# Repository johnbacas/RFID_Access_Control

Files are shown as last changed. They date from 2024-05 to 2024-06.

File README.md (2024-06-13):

## **RFID Access control Project**

Περιγραφή: Το σύστημα αυτό είναι σχεδιασμένο ώστε να κάνει έλεγχο πρόσβασης με χρήση RFID tags.
Η μονάδα ελέγχου που χρησιμοποιείται είναι η πλακέτα NodeMCU με τον μικροελεγκτή (SoC) ESP8266 με δυνατότητα σύνδεσης στο Internet μέσω WiFi.

[Πληροφορίες για esp8266](https://www.espressif.com/en/products/socs/esp8266)

[Πληροφορίες για NodeMCU](https://www.nodemcu.com/index_en.html)

Σαν RFID reader χρησιμοποιήθηκε το module RC-522

[Πληροφορίες για RFID RC-522](https://lastminuteengineers.com/how-rfid-works-rc522-arduino-tutorial/)

**ΠΡΟΣΟΧΗ...!!!**
Αποθήκευση ετικετών: Επειδή ο μικροελεγκτής esp8266 **δεν έχει** μνήμη EEPROM, όλες οι εγγραφές που φαίνεται στο πρόγραμμα ότι γίνονται σε EEPROM στην πραγματικότητα γίνονται στη μνήμη Flash του μικροελεγκτή (Η μνήμη στην οποία αποθηκεύεται και το πρόγραμμα).
Αυτό σημαίνει ότι οι επαναλαμβανόμενες εγγραφές στη μνήμη EEPROΜ φθείρουν τη μνήμη Flash.
Άρα το project αυτό καλό είναι να χρησιμοποιείται σε εφαρμογές όπου δεν θα γίνονται συχνά εγγραφές στη μνήμη EEPROM (Flash).

Δείτε περισσότερες πληροφορίες [εδώ](https://www.aranacorp.com/en/using-the-eeprom-with-the-esp8266/).

Υπάρχουν κάποιες βιβλιοθήκες που ελαχιστοποιούν τη φθορά της μνήμης Flash. Δείτε μια λύση [εδώ](https://www.arduino.cc/reference/en/libraries/esp_eeprom/).

**Α) Λειτουργία προγραμματισμού: ( το μπλε led αναβοσβήνει με γρήγορο ρυθμό)**

 - Ορισμός master tag

Ο εγκαταστάστης του συστήματος έχει τη δυνατότητα να ορίσει ένα master tag, μέσω του οποίου μπορεί να προσθέτει και να αφαιρεί tags από την λίστα των tags που έχουν πρόσβαση.
Όταν το σύστημα τίθεται σε λειτουργία την πρώτη φορά, ζητάει από τον προγραμματιστή να ορίσει ποιο είναι το *master tag*. Στη συνέχεια ο προγραμματιστής πλησιάζει στο RFID Reader το tag που θέλει να ορίσει σαν master. Το master tag αποθηκεύεται στη μνήμη του συστήματος.

 - Προσθήκη ή αφαίρεση tag από την λίστα πρόσβασης

Ο προγραμματιστής αρχικά χρησιμοποιεί το master tag για να μπει σε programming mode. Στη συνέχεια πλησιάζει στον reader ένα tag. Αν αυτό δεν υπάρχει στη λίστα πρόσβασης τότε προστίθεται (το πράσινο led αναβοσβήνει 3 φορές) , ενώ αν υπάρχει τότε αφαιρείται ( τα μπλε και πράσινο leds αναβοσβήνουν 3 φορές). Αν για κάποιο λόγο η εγγραφή δεν πραγματοποιηθεί τότε το μπλε led αναβοσβήνει 3 φορές και το buzzer ηχεί 3 φορές επίσης.

**Β) Λειτουργία ελέγχου πρόσβασης: ( το μπλε led αναβοσβήνει με αργό ρυθμό)**

Ο χρήστης πλησιάζει το tag του στον reader. Αν το σύστημα έχει αποθηκευμένο τον κωδικό του tag αυτού τότε δίνει εντολή ώστε να δωθεί πρόσβαση (μεσω της ενεργοποίησης της ηλεκτρικής κλειδαριάς). Αν ο κωδικός δεν είναι αποθηκευμένος, το σύστημα ενημερώνει με ήχο τον χρήστη ότι δεν έχει πρόσβαση.

Ανεξαρτήτως λειτουργίας, κάθε φορά που διαβάζεται ένα tag από τον reader το πράσινο led ανάβει για 0,5 sec.

SCHEMATIC:

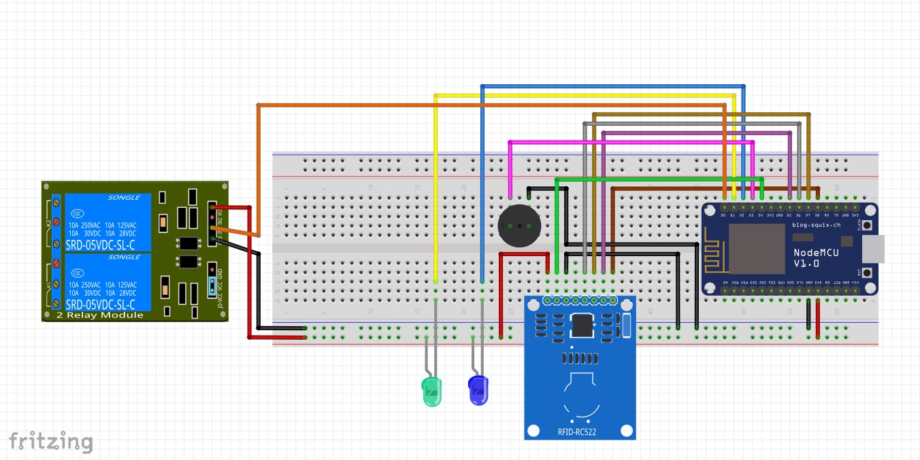
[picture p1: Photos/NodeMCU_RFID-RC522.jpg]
RFID_Access_Control_Img


**Blynk Console - Εφαρμογή ειδοποιήσεων και καταγραφής των περιστατικών προσπάθειας πρόσβασης**

Ο εγκαταστάστης του συστήματος έχει πρόσβαση στο περιβάλλον Blynk (Πλατφόρμα εφαρμογών IOT). Στο dashboard υπάρχει widget τύπου terminal που καταγράφει τα περιστατικά προσπάθειας πρόσβασης.
Στο terminal καταγράφονται η ημερομηνία και η ώρα της πρόσβασης, και αν η πρόσβαση ήταν επιτυχής ή οχι. Επίσης γίνεται καταγραφή της χρήσης master card στο σύστημα.
Παρακάτω φαίνεται ένα παράδειγμα καταγραφής.

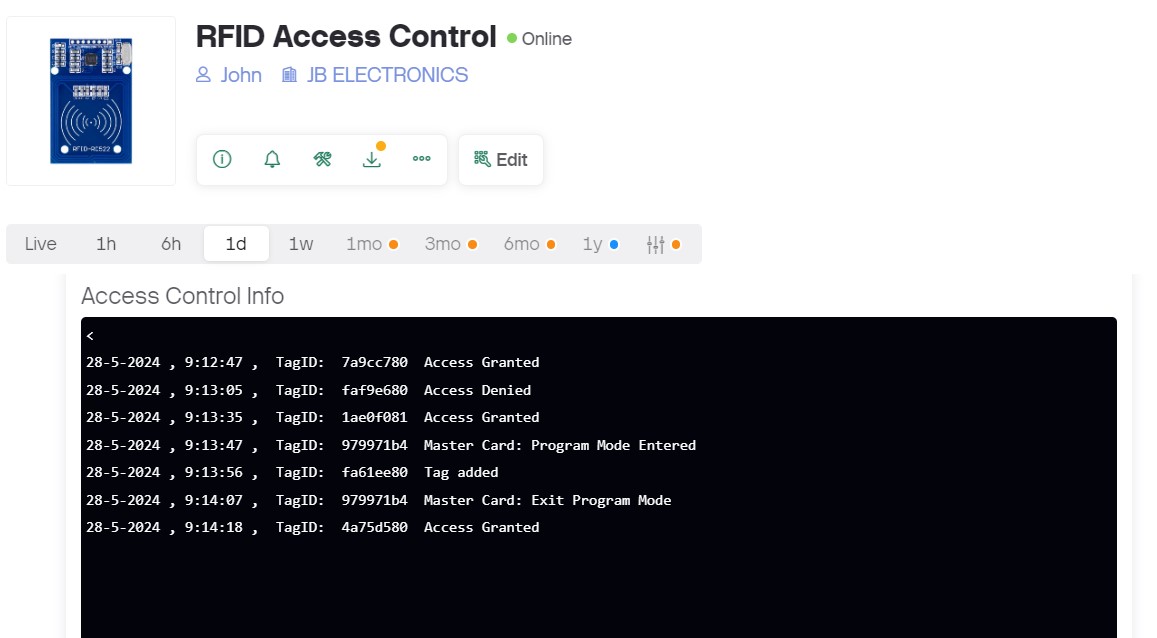
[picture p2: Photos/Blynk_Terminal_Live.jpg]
Blynk Terminal


Για να δημιουργήσετε το συσγκεκριμένο dashboard θα πρέπει να δημιουργήσετε ένα λογαρισμό στην εφαρμογή Blynk και στη συνέχεια, μπαίνοντας στο developer zone, να δημιουργήσετε ένα νεο template και στη συνέχεια ένα νεο Device.
Εισάγετε το widget Terminal με τις παρακάτω ρυθμίσεις.

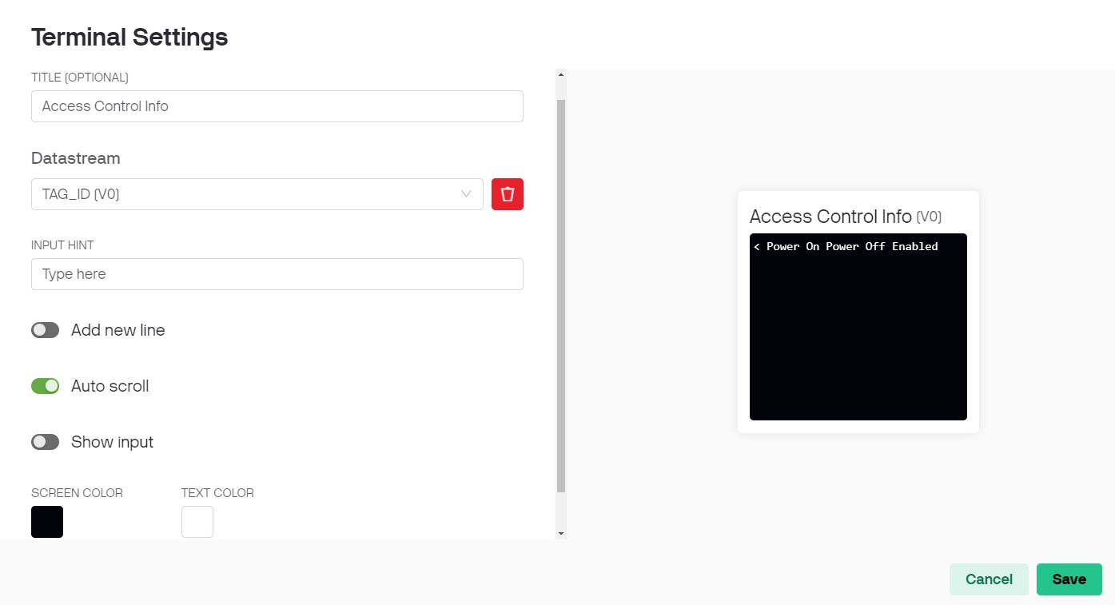
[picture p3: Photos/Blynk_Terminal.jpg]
Blynk Terminal Configure


Επίσης, μην ξεχάσετε να προσθέσετε και ένα event ώστε να έχετε logging υπηρεσία στην εφαρμογή σας.

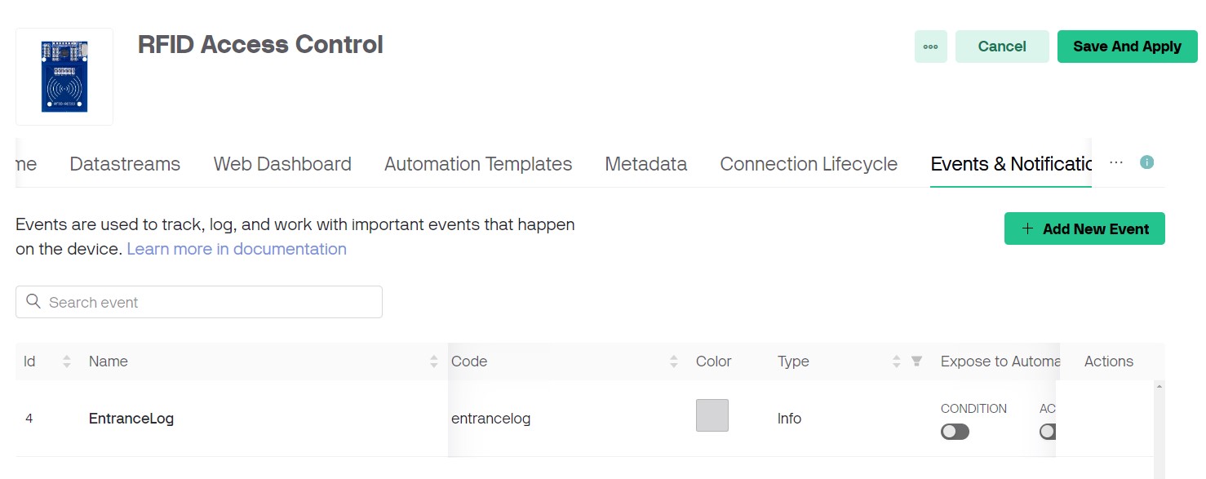
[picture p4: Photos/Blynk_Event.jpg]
Blynk Event


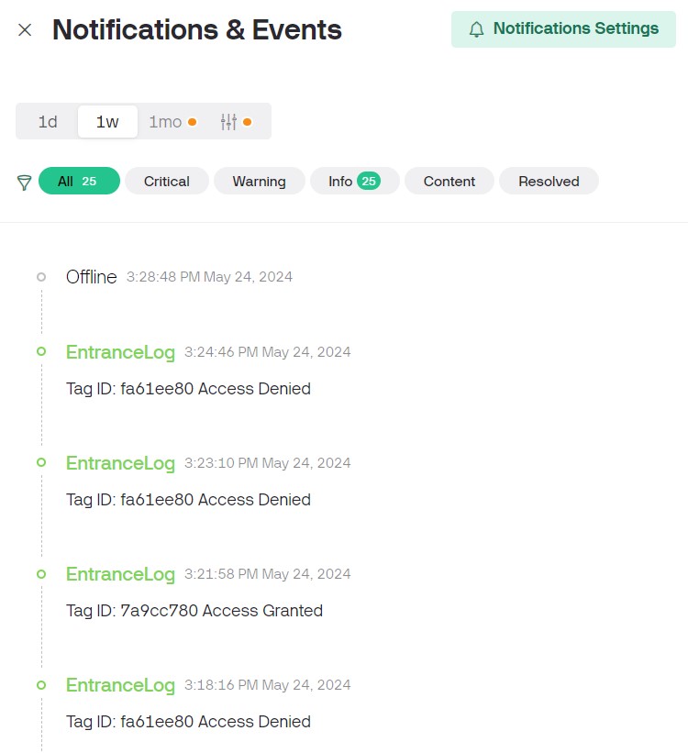
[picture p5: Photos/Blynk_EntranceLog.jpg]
Blynk Log


Αν έχετε απορίες για το πως θα στήσετε την πρώτη σας εφαρμογή στο Blynk δείτε [εδώ](https://docs.blynk.io/en/getting-started/what-do-i-need-to-blynk)

Δείτε ένα [βίντεο](https://youtu.be/cB8p_oedzpM?si=Qd5MNCRZdafjuK6v) που εξηγεί την λειτουργία του κυκλώματος.

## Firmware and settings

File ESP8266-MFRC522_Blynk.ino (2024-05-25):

/************************************************************************
  This is an access control project using a NodeMCU and CR522 RFID reader.
  It uses "Blynk" as an IOT for exchanging information with NodeMCU
  and controlling access through smart phone or PC
  Creator: JOHN BACAS  (john.bacas@gmail.com)
 ***********************************************************************/

/* wiring the MFRC522 to ESP8266 (ESP-12)
RST     = GPIO0
SDA(SS) = GPIO2 
MOSI    = GPIO13
MISO    = GPIO12
SCK     = GPIO14
GND     = GND
3.3V    = 3.3V
*/
 // BLYNK.console Home - FirmWare Configuration
#define BLYNK_TEMPLATE_ID ""
#define BLYNK_TEMPLATE_NAME ""
#define BLYNK_AUTH_TOKEN ""

/* Comment this out to disable prints and save space */
#define BLYNK_PRINT Serial

#include <ESP8266WiFi.h>
#include <BlynkSimpleEsp8266.h>
#include <TimeLib.h>
#include <WidgetRTC.h>
#include <EEPROM.h> 
#include <SPI.h>
#include "MFRC522.h"

#define LED_ON LOW
#define LED_OFF HIGH
//#define redLed 16
#define greenLed 5
#define blueLed 4
#define relay 16
#define buzzer 0

boolean match = false; 
boolean programMode = false; 
int successRead; 

byte storedCard[4];  
byte readCard[4];
byte masterCard[4];

String tag = "";

#define RST_PIN	2  // RST-PIN for RC522 - RFID - SPI - GPIO2 - D4
#define SS_PIN	15  // SDA-PIN for RC522 - RFID - SPI - GPIO15 - D8

String currentTime;
String currentDate;

const char *ssid =	"YOUR NETWORK SSID";	    // change according to your Network
const char *pass =	"YOUR NETWORK PASSWORD";	// change according to your Network


MFRC522 mfrc522(SS_PIN, RST_PIN);	// Create MFRC522 instance
BlynkTimer timer;
WidgetRTC rtc;
WidgetTerminal terminal(V0);

int ledState = LOW;
long slowFlashing = 1200;
long fastFlashing = 150;
unsigned long previousMillis = 0;
//const long interval = 1200; // blue led flashing interval

BLYNK_CONNECTED() {
  // Synchronize time on connection
  rtc.begin();
}


void setup() {       //*********************** SETUP ***************************
  pinMode(greenLed, OUTPUT);
  pinMode(blueLed, OUTPUT);
  pinMode(relay, OUTPUT);
  pinMode(buzzer, OUTPUT);
  
  digitalWrite(relay, HIGH);
  digitalWrite(greenLed, LED_OFF);
  digitalWrite(blueLed, LED_OFF);
  
  Serial.begin(9600);    // Initialize serial communications
  SPI.begin();	         // Init SPI bus
  mfrc522.PCD_Init();    // Init MFRC522
  mfrc522.PCD_SetAntennaGain(mfrc522.RxGain_max);
  
  Blynk.begin(BLYNK_AUTH_TOKEN, ssid, pass);
  setSyncInterval(10 * 60); // Sync interval in seconds (10 minutes)
  delay(200);
  
  EEPROM.begin(512);
  byte check;
  EEPROM.get(1,check);
  if (check != 143) { 
    Serial.println("No Master Card Defined");
    Serial.println("Scan A PICC to Define as Master Card");
    do {
      successRead = getID();
      ledFlashing(fastFlashing);  // program mode: blue led fast flashing
    } while (!successRead);
    
    for ( int j = 0; j < 4; j++ ) { 
      EEPROM.put( 2 + j, readCard[j] ); 
    }
    EEPROM.put(1, byte(143));
    EEPROM.commit();
    Serial.println("Master Card Defined");
  }
  
  Serial.print("Master Card's UID: ");
  for ( int i = 0; i < 4; i++ ) {     
    EEPROM.get(2 + i, masterCard[i]); 
    Serial.print(masterCard[i], HEX);
  }
  
  Serial.println("");
  readEEPROM();
  Serial.println("");
  //Blynk.run();
  //timer.run();
  Serial.println("Waiting PICCs to be scanned :)");
  ledFlashing(slowFlashing);  // normal mode: blue led slow flashing
}


void loop() {        //************************ LOOP *********************************
  
  do {
    Blynk.run();
    timer.run();
    successRead = getID(); 
    if (programMode) {
      ledFlashing(fastFlashing);  // program mode: blue led fast flashing
    }
    else {
      ledFlashing(slowFlashing); // normal mode: blue led slow flashing
    }
  }
  while (!successRead);
 
  if (programMode) {
    if ( isMaster(readCard) ) { 
      Serial.println("This is Master Card");
      Serial.println("Exiting Program Mode");
      Serial.println("-----------------------------");
      Blynk.virtualWrite(V0, " Master Card: Exit Program Mode ");
      programMode = false;
      return;
    }
    else {
      if ( findID(readCard) ) { 
        Serial.println("I know this PICC, so removing");
        deleteID(readCard);
        Serial.println("-----------------------------");
        Blynk.virtualWrite(V0, " Tag removed ");
      }
      else { 
        Serial.println("I do not know this PICC, adding...");
        writeID(readCard);
        Serial.println("-----------------------------");
        Blynk.virtualWrite(V0, " Tag added ");
      }
    }
  }
  else {
    if ( isMaster(readCard) ) {  
      programMode = true;
      Serial.println("Hello Master - Entered Program Mode");
      Blynk.virtualWrite(V0, " Master Card: Program Mode Entered ");
      byte count;
      EEPROM.get(0, count); 
      Serial.print("I have ");  
      Serial.print(count);
      Serial.print(" record(s) on EEPROM");
      Serial.println("");
      readEEPROM();
      Serial.println("Scan a PICC to ADD or REMOVE");
      Serial.println("-----------------------------");
    }
    else {
      if ( findID(readCard) ) { 
        Serial.println("Welcome, You shall pass");
        Blynk.virtualWrite(V0, " Access Granted ");
        Serial.println("----------------------------");
        Blynk.logEvent("entrancelog", String("Tag ID: ") + tag + String("  Access Granted"));
        //digitalWrite(greenLed, LED_ON);
        digitalWrite(relay, LOW);
        delay(1200);
        //digitalWrite(greenLed, LED_OFF);
        digitalWrite(relay, HIGH);
      }
      else {     
        Serial.println("You shall not pass");
        Blynk.virtualWrite(V0, " Access Denied ");
        Serial.println("----------------------------");
        Blynk.logEvent("entrancelog", String("Tag ID: ") + tag + String("  Access Denied"));
        //digitalWrite(greenLed, LED_ON);
        digitalWrite(buzzer, HIGH);
        delay(1200);
        //digitalWrite(greenLed, LED_OFF);
        digitalWrite(buzzer, LOW);
      }
    }
  }
}

// ********************************** FUNCTIONS ************************************
int getID() {
  if ( ! mfrc522.PICC_IsNewCardPresent()) {
    delay(70);
    return 0;
  }
  if ( ! mfrc522.PICC_ReadCardSerial()) {
    delay(70);
    return 0;
  }
  int minutes = minute();
  int seconds = second();
  currentTime = String(hour()) + ":";
  currentTime += (minutes<10)? "0" + String(minutes) + ":" : String(minutes) + ":";
  currentTime += (seconds<10)? "0" + String(seconds) + " , " : String(seconds)+ " , ";
  currentDate = String(day()) + "-" + month() + "-" + year() + " , ";  
  tag="";
  Serial.print("Scanned PICC's UID: ");
  for (int i = 0; i < 4; i++) { 
    readCard[i] = mfrc522.uid.uidByte[i];
    Serial.print(readCard[i], HEX);
    tag += String(readCard[i], HEX);    
  }
  Blynk.virtualWrite(V0, "\n" + currentDate + currentTime + " TagID: ");
  Blynk.virtualWrite(V0, tag);
  //Blynk.logEvent("entrancelog", String("Tag ID: ") + tag);
  Serial.println("");
  mfrc522.PICC_HaltA();
  digitalWrite(blueLed, LED_OFF);
  digitalWrite(greenLed, LED_ON);
  delay(500);
  digitalWrite(greenLed, LED_OFF);
  return 1;
}


void ledFlashing (long interval) {
  unsigned long currentMillis = millis();
  if (currentMillis - previousMillis >= interval) {
  previousMillis = currentMillis;
    if (ledState == LOW) {
      ledState = HIGH;
    } else {
      ledState = LOW;
    }
  digitalWrite(blueLed, ledState);
  } 
}


void readID( int number ) {
  int start = (number * 4 ) + 2; 
  for ( int i = 0; i < 4; i++ ) { 
    EEPROM.get(start + i, storedCard[i]); 
  }
}


void writeID( byte a[] ) {
  if ( !findID( a ) ) {
    byte num;
    EEPROM.get(0, num); 
    int start = ( num * 4 ) + 6;
    num++;
    EEPROM.put( 0, num );
    for ( int j = 0; j < 4; j++ ) {
      EEPROM.put( start + j, a[j] );
    }
    EEPROM.commit();
    successWrite();
  }
  else {
    failedWrite();
  }
}


void deleteID( byte a[] ) {
  if ( !findID( a ) ) { 
    failedWrite();
  }
  else {
    byte num;
    EEPROM.get(0, num);
    //int slot;
    //int start;
    //int looping;
    int j=0;
    int slot = findIDSLOT( a );
    int starting = (slot * 4) + 2;
    int looping = (num - slot) * 4;
     
    //char buf[40];
    //sprintf(buf, "Slot: %d, starting: %d, looping: %d", slot, starting, looping);
    //Serial.println(buf);
  
    num--;
    EEPROM.put( 0, num );
    for ( j = 0; j < looping; j++ ) {
      byte record;
      EEPROM.get(starting + 4 + j, record);
      EEPROM.put(starting + j, record);
    }
    for ( int k = 0; k < 4; k++ ) {
      EEPROM.put( starting + j + k, byte(0));
    }
    EEPROM.commit();
    successDelete();
  }
}


boolean checkTwo ( byte a[], byte b[] ) {
  if ( a[0] != NULL )
    match = true;
  for ( int k = 0; k < 4; k++ ) { 
    if ( a[k] != b[k] )
      match = false;
  }
  if ( match ) {
    return true; 
  }
  else  {
    return false; 
  }
}


int findIDSLOT( byte find[] ) {
  byte count;
  EEPROM.get(0, count); 
  for ( int i = 1; i <= count; i++ ) {
    readID(i); 
    if ( checkTwo( find, storedCard ) ) {    
      return i;
      break;
    }
  }
  return int(count+1);
}


boolean findID( byte find[] ) {
  byte count;
  EEPROM.get(0,count);
  for ( int i = 1; i <= count; i++ ) {
    readID(i);
    if ( checkTwo( find, storedCard ) ) {
      return true;
      break;
    }
//    else {
//    }
  }
  return false;
}

void successWrite() {  // green led flases 3 times
  digitalWrite(blueLed, LED_OFF);
  digitalWrite(greenLed, LED_OFF);
  delay(100);
  digitalWrite(greenLed, LED_ON);
  delay(100);
  digitalWrite(greenLed, LED_OFF);
  delay(100);
  digitalWrite(greenLed, LED_ON);
  delay(100);
  digitalWrite(greenLed, LED_OFF);
  delay(100);
  digitalWrite(greenLed, LED_ON);
  delay(100);
  digitalWrite(greenLed, LED_OFF);
  Serial.println("Succesfully added ID record to EEPROM");
}

void failedWrite() {  // blue led flashes 3 times
  digitalWrite(blueLed, LED_OFF);
  digitalWrite(greenLed, LED_OFF);
  delay(100);
  digitalWrite(blueLed, LED_ON);
  digitalWrite(buzzer, HIGH);
  delay(100);
  digitalWrite(blueLed, LED_OFF);
  digitalWrite(buzzer, LOW);
  delay(100);
  digitalWrite(blueLed, LED_ON);
  digitalWrite(buzzer, HIGH);
  delay(100);
  digitalWrite(blueLed, LED_OFF);
  digitalWrite(buzzer, LOW);
  delay(100);
  digitalWrite(blueLed, LED_ON);
  digitalWrite(buzzer, HIGH);
  delay(100);
  digitalWrite(blueLed, LED_OFF);
  digitalWrite(buzzer, LOW);
  Serial.println("Failed! There is something wrong with ID or bad EEPROM");
}

void successDelete() {  // blue and green leds flash 3 times
  digitalWrite(blueLed, LED_OFF);
  digitalWrite(greenLed, LED_OFF);
  delay(100);
  digitalWrite(blueLed, LED_ON);
  digitalWrite(greenLed, LED_ON);
  delay(100);
  digitalWrite(blueLed, LED_OFF);
  digitalWrite(greenLed, LED_OFF);
  delay(100);
  digitalWrite(blueLed, LED_ON);
  digitalWrite(greenLed, LED_ON);
  delay(100);
  digitalWrite(blueLed, LED_OFF);
  digitalWrite(greenLed, LED_OFF);
  delay(100);
  digitalWrite(blueLed, LED_ON);
  digitalWrite(greenLed, LED_ON);
  delay(100);
  digitalWrite(blueLed, LED_OFF);
  digitalWrite(greenLed, LED_OFF);
  Serial.println("Succesfully removed ID record from EEPROM");
}

boolean isMaster( byte test[] ) {
  if ( checkTwo( test, masterCard ) )
    return true;
  else
    return false;
}


void readEEPROM(){
  Serial.print("Records:");
  byte num = EEPROM.read(0);
  for (int i = 6; i < num * 4 + 6; i++){
    if (i % 4 == 2){      
      Serial.println("");
      Serial.print(String((i-2) / 4)+ ") ");
    }
    byte data = EEPROM.read(i);
    Serial.print(data, HEX);
    Serial.print(" ");
  }
  Serial.println("");
}
